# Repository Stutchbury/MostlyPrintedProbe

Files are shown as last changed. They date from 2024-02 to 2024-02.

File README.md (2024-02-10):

# A Mostly Printed Probe
A mostly printed kinetic probe for CNC machines that can be fully 3D printed (or turned on a lathe) and requires no soldering.

>If you can't make it accurate, make it adjustable.

3D printing accuracy is often hard to achieve, especially on a variety of printers, but this probe has been designed to work within the those accuracy contraints and has proven to provide remarkable repeatability:

Mostly Printed Probe first test (https://www.youtube.com/embed/06nPOA94Pbk)

After my 21 year old ebay 'bargain' Renishaw gave up the ghost, I needed a probe quickly to continue developing my [CNC Probe Interface](https://github.com/Stutchbury/CNCProbeInterface) so designed one to turn on the lathe but the test 3D printed version worked so well, it is now an official side project...

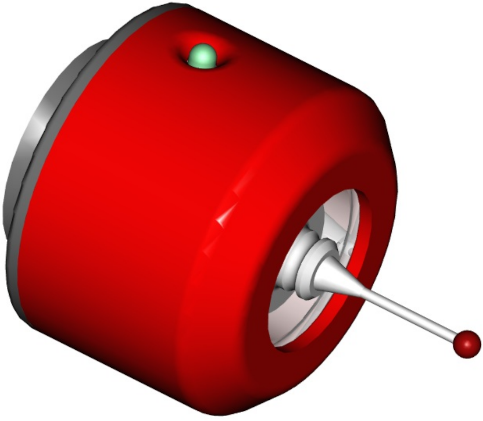
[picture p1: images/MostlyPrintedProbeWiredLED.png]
MostlyPrintedProbeWiredLED


With the exception of the 3mm diameter pins and the stylus, all of this probe is able to be FDM printed - even the spring is made from a length of filament! Only one part (the top) requires supports.

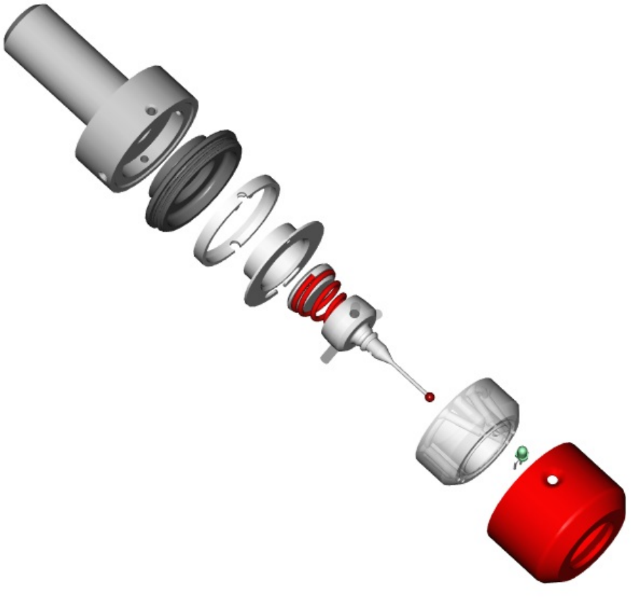
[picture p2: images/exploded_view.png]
MostlyPrintedProbeExploded


The 25mm/30° taper in the top allows concentricity to be tuned in on a mandrel while the tapered interface between body and sleeve ensure concentricity is maintained. 

There are two different bodies - one is wired only and the second can also accommodate a 3mm LED (single or bi-colour). The non-LED version requires no soldering.

This is the first build, it is fairly compact at 38mm diameter x 28mm tall. 

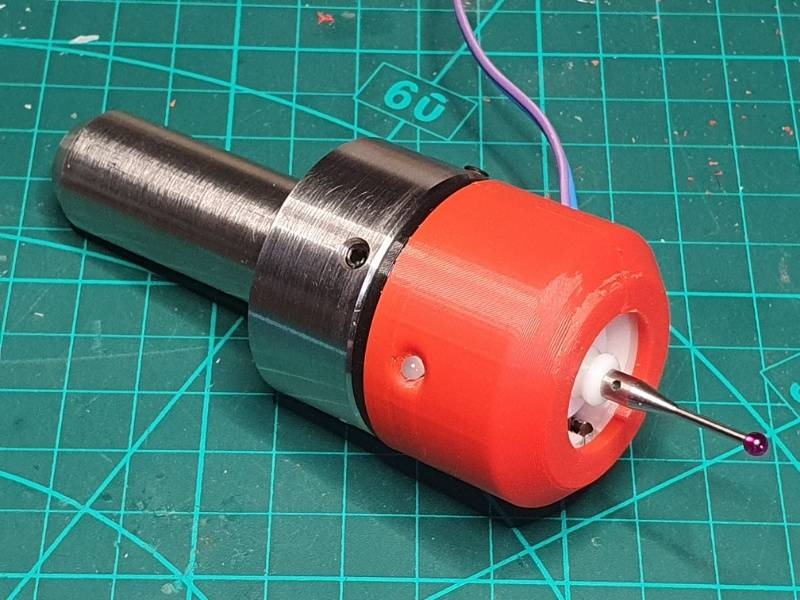
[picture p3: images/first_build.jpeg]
first buid


As with all mechanical kinetic probes, this will work best with a [resistive switching interface](https://github.com/Stutchbury/CNCProbeInterface) but will also work fine as a plain old NC (normally closed) switch.

## Materials & Tools Required

A quick list of things you'll need - I will create a proper print/build guide VSN.

- **Pins** - I have used 3mm tungsten carbide rods, but any decently conductive metal would work and is probably a lot easier to cut. Search for "3mm dowel pins" for pre-cut hardened steel ones.

  - 9off 3mm diameter by 11.5mm - 12mm length.

- **Filament** - I used plain old PLA on a rather old & tired Ender 3.

- **Accurate 3mm drill** or reamer (measure your drills, they vary a lot).

- **M3 tap** - to fit the stylus and optionally the spring tensioner.

- **Thin stranded wire** - as fine as you can. I stripped out a ribbon cable but old USB charging cables are a good source.

All the STLs are available [here](stl/). There are also 12mm and 3/4" example mandrels for fitting into your spindle. These enable concentricity to be tuned in.

## Slicing and Printing

A slicing and printing guide is available [here](docs/PRINTING.md).

## Assembly

The [assembly guide](docs/ASSEMBLY.md) is curently a work in progress.

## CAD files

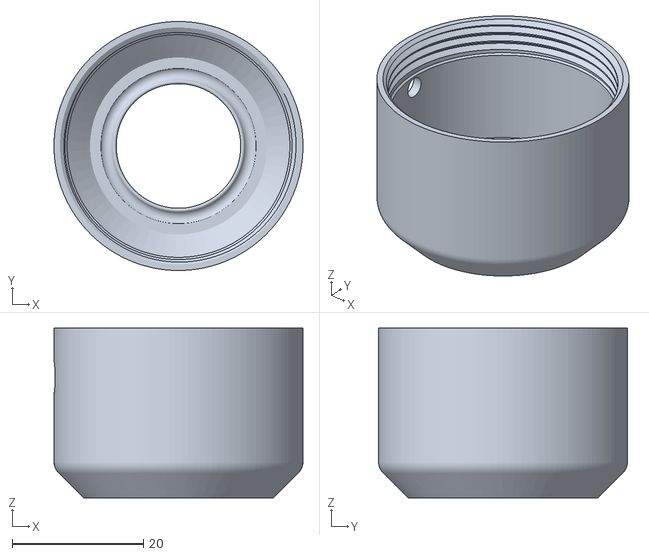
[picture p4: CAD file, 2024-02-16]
stl/MostlyPrintedProbe-PartMainBodyWired.stl
38.0 x 38.0 x 25.9

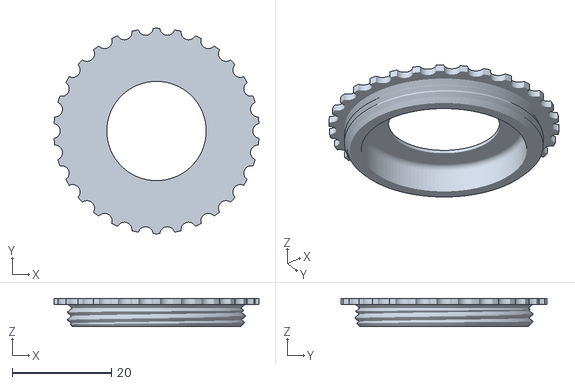
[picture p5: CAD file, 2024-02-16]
stl/MostlyPrintedProbe-PartTestExternalThread.stl
41.3 x 41.4 x 5.70

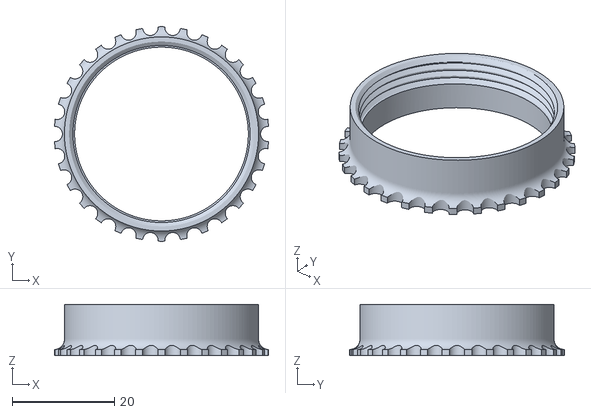
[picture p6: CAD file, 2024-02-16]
stl/MostlyPrintedProbe-PartTestInternalThread.stl
41.9 x 42.0 x 10.0

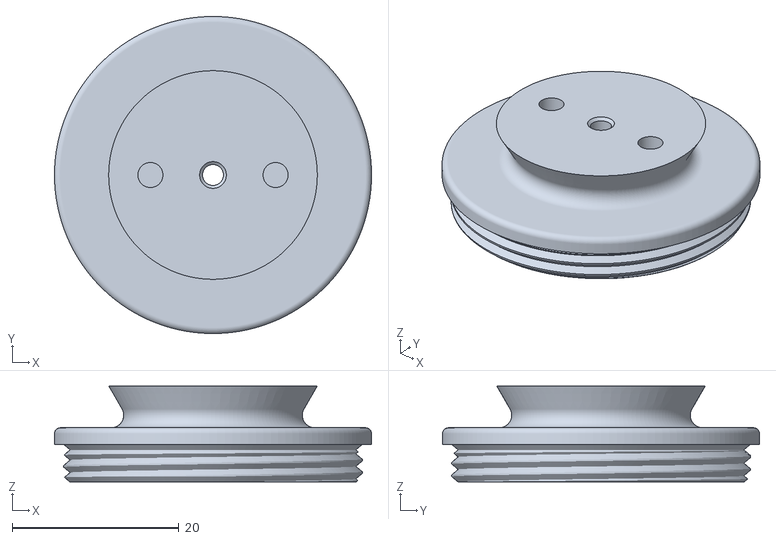
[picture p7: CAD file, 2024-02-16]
stl/MostlyPrintedProbe-PartTop.stl
38.0 x 38.0 x 11.5

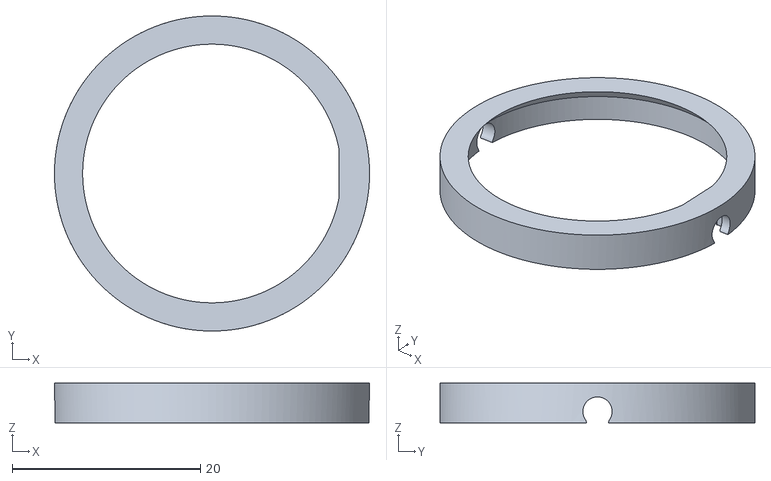
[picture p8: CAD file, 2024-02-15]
stl/MostlyPrintedProbe-PartSpacerWired.stl
33.5 x 33.5 x 4.20

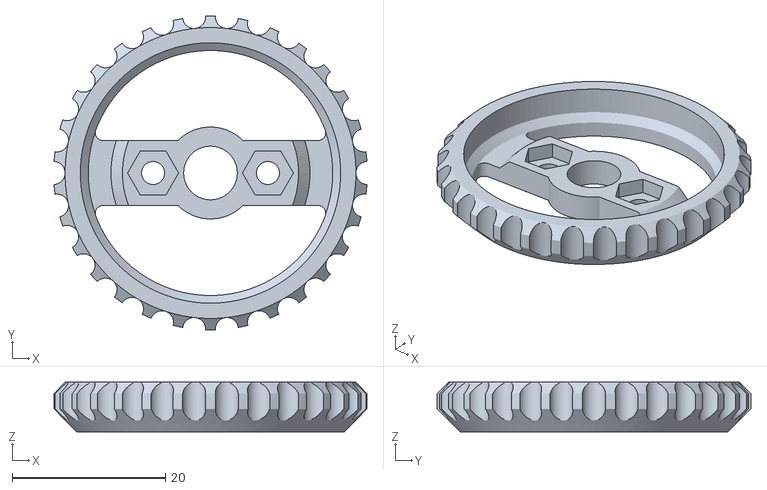
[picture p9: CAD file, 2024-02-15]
stl/MostlyPrintedProbe-ParLidSpanner.stl
40.9 x 41.0 x 6.50

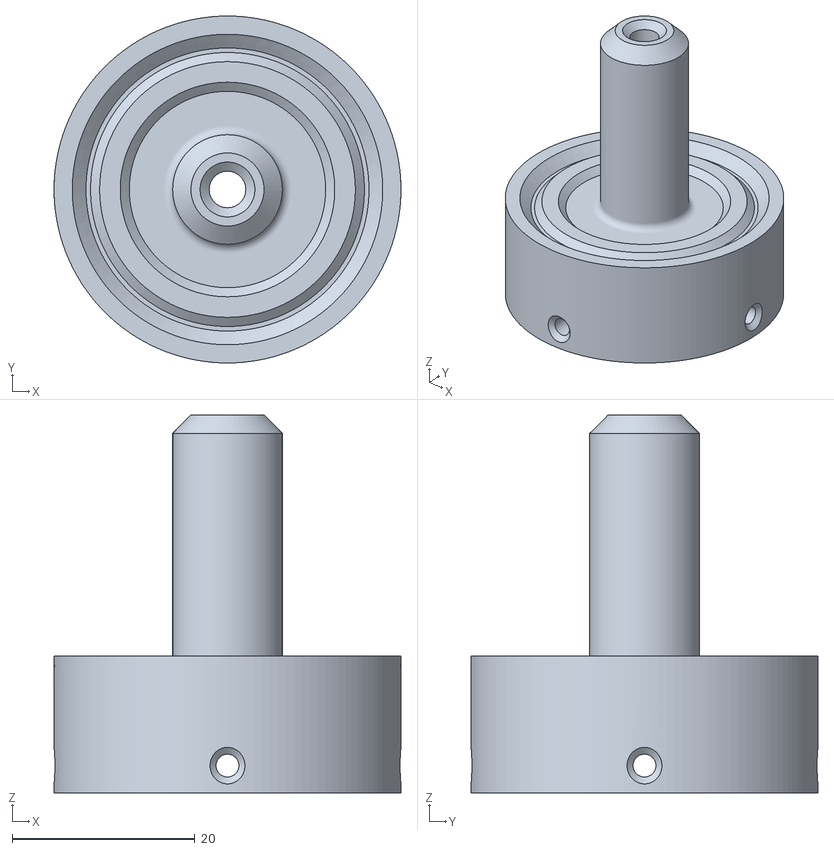
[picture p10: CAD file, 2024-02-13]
stl/MostlyPrintedProbe-PartSpindleMandrel-12mm.stl
38.0 x 38.0 x 41.4

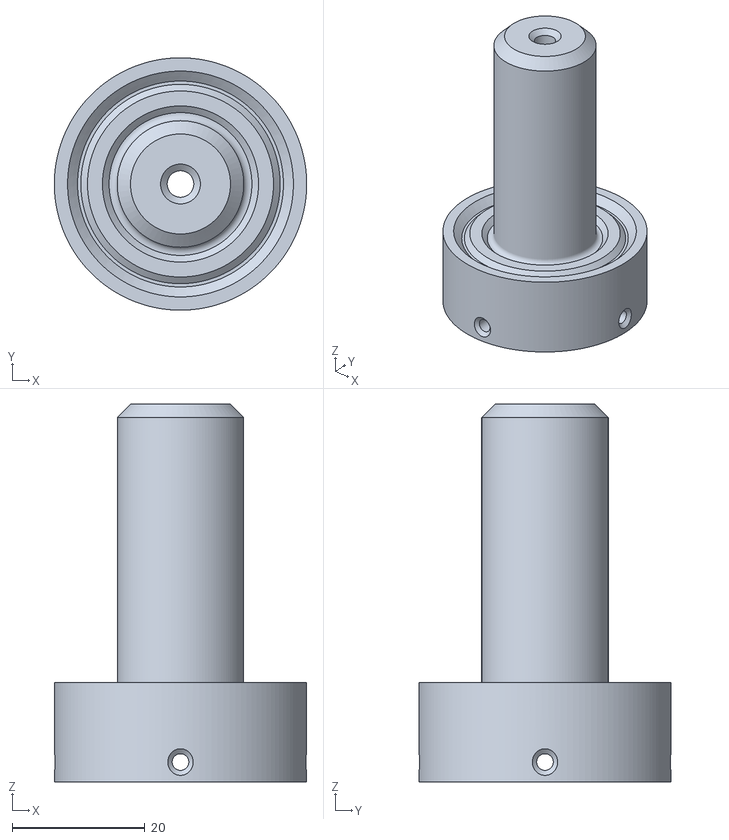
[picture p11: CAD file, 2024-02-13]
stl/MostlyPrintedProbe-PartSpindleMandrel-TTS.stl
38.0 x 38.0 x 56.9

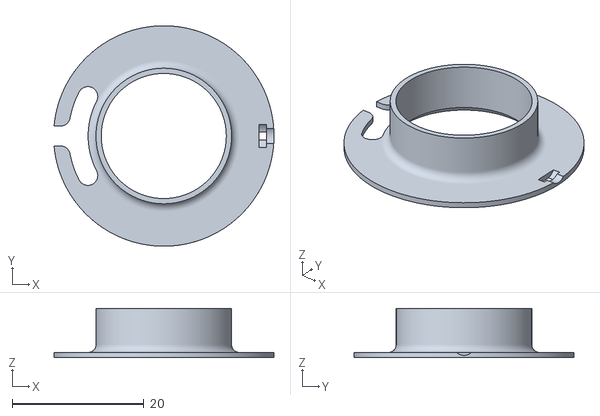
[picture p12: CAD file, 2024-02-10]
stl/MostlyPrintedProbe-PartPinsCover.stl
33.4 x 33.5 x 7.50

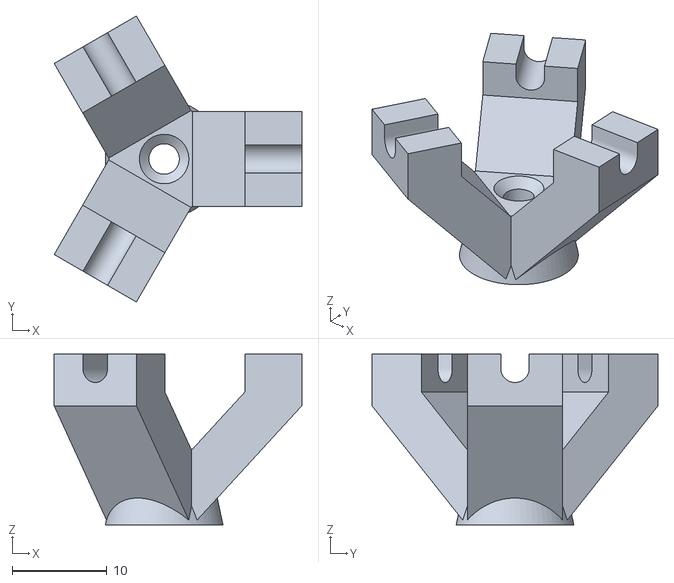
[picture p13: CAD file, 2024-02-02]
stl/MostlyPrintedProbe-PartSpiderTappingTool.stl
26.1 x 30.1 x 18.0

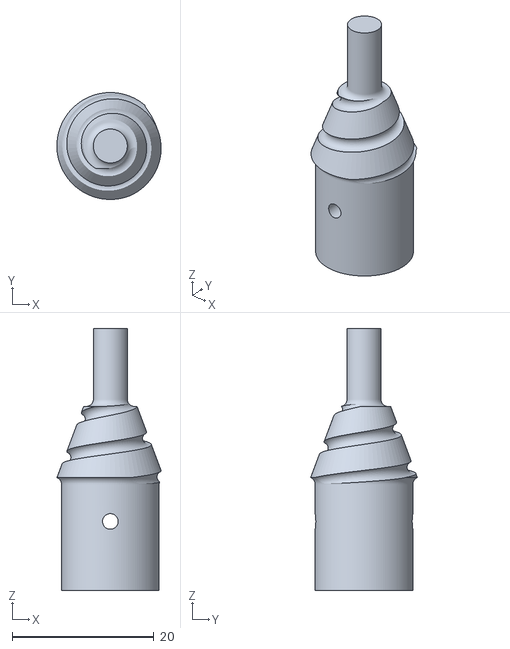
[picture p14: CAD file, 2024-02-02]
stl/MostlyPrintedProbe-PartSpringMandrel.stl
14.7 x 15.1 x 37.0

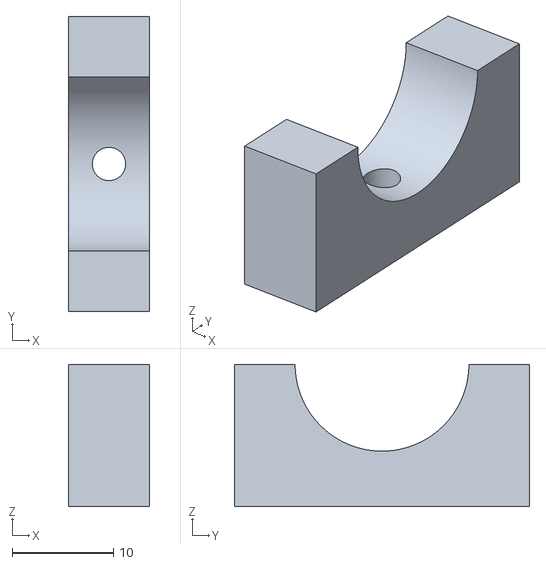
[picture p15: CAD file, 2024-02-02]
stl/MostlyPrintedProbe-PartSpiderPinTool.stl
8.00 x 29.2 x 14.1

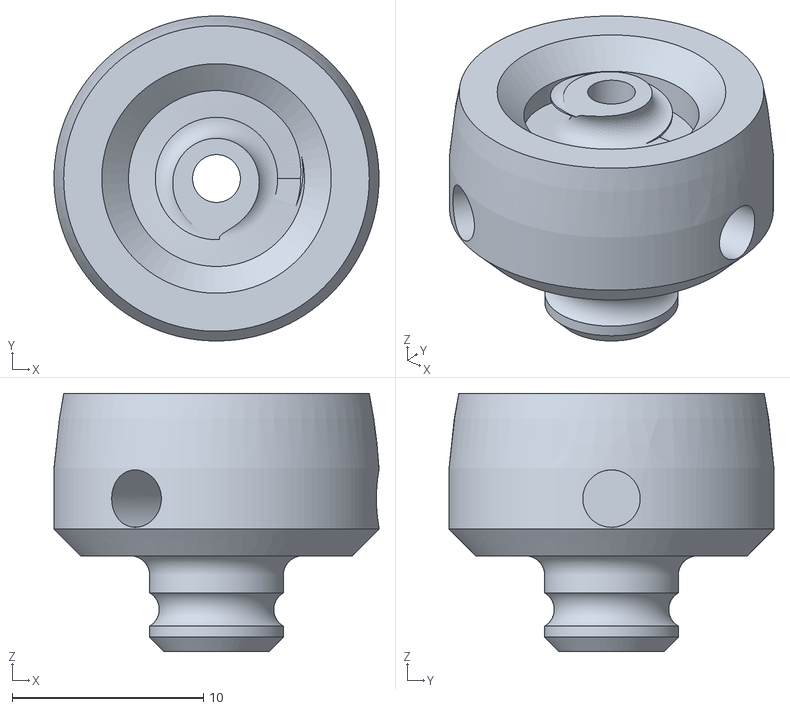
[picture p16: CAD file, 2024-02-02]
stl/MostlyPrintedProbe-PartSpider.stl
17.0 x 17.0 x 13.5

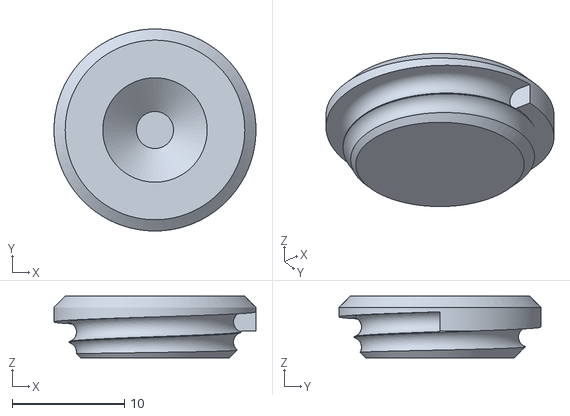
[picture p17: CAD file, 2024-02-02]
stl/MostlyPrintedProbe-PartSpringTop.stl
18.0 x 18.0 x 5.50

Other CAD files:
stl/MostlyPrintedProbe-PartMainBodyWiredLED.stl

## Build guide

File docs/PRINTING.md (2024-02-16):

# Printing the Mostly Printed Probe

This guide is for FDM printing the Mostly Printed Probe. All models are [here](../stl).

## Tolerances

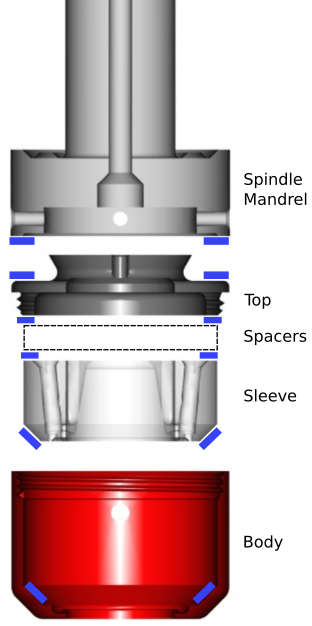
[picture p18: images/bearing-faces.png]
bearing face


Most of the models have fairly relaxed tolerances with the accuracy of the probe being defined by the bearing faces shown above in blue - in particular, the 45° faces inside the body and on the bottom of the sleeve.

### Threads

Yes, the large threads work just fine in a 3D printed model!

The M3 threads in the lid (for the spring tension) and spider (for the stylus) need to be carefully cut with a tap. A [threading guide](../stl/MostlyPrintedProbe-PartSpiderTappingTool.stl) is provided to help align the tap with the spider.

The main M36 x 1.5mm thread (that secures the top to the body and compresses all the bearing faces) can provide some challenges. The thread itself has a generous tolerance built in, but there are many factors to acheiving a good thread but all can be resolved in the slicer.

Note: The main threads are now at an 80° thread angle rather than the standard 60° - this helps printing overhangs without support.

#### Shrinkage
The first lid & body I printed fitted perfectly (yes, I know, I'm was as surprised as you are) but when I re-printed the body in red, the diameter shrank. The same filament from the same manufacturer but in black, did not.

I have created two test nodels that I suggest are printed with your filament of choice. There is an [internal thread](../stl/MostlyPrintedProbe-PartTestInternalThread.stl) to represent the main body and an [external thread](../stl/MostlyPrintedProbe-PartTestExternalThread.stl) for the lid.

Print the internal thread (or the main body if you're feeling confident) first and then match the external thread to it. If your filament is similar to mine, it should fit first time, otherwise, scale and re-print the external thread and apply these settings to the lid slicing. Clean up the seam inside the thread hollows and lubricate with a soft pencil to prevent the stickyness of some filaments.

The test prints have grips on the perimeter but if you get the real lid stuck, there's a [spanner](../stl/MostlyPrintedProbe-ParLidSpanner.stl) for it!

#### Sagging
If your filament is too hot, the thread overhangs ~~(they are at 60°)~~ can sag a little, so playing with the temperature can help. The new 80° thread angle should significantly mitigate this issue.

#### Sticktion
Some filaments, especially shiny PLA, have a nasty habit of sticking to each other. Your thread may be perfect but the think just wants to stick. Matt PLA seems to work much better.

Use graphite (a soft pencil) to lubticate the threads and make sure the seams is cleaned out of the thread grooves.

Use the lid spanner to free a stuck thread.

#### Cross threading

An M36 x 1.5mm thread is *really* easy to cross thread - especially when the wires are not allowing the spacers to sit flat. Check the thread works wih just the lid and body (I'm sure you would anyway...) but be exceedingly careful as once cross threaded, plastic threads are very difficult to 'get back'. If it doesn't start easily & reliably, then final assembly gets a bit fractious.

## Slicing & Printing

I'm using Cura at 0.2mm layer height. Sometimes the slicer will report errors in the STLs but then automagically repair them and print just fine. I'm working on resolving this but as everything prints OK, it is a little down the priority list.

**A Note on Seams:** Unless you are able to truly hide your Z seam (ie no blobs), I recommend having a single seam that can be filed or scraped flat where required.

Unless otherwise specified, I am using 4 walls and the default infill. Only one part need supports.

### Sleeve 

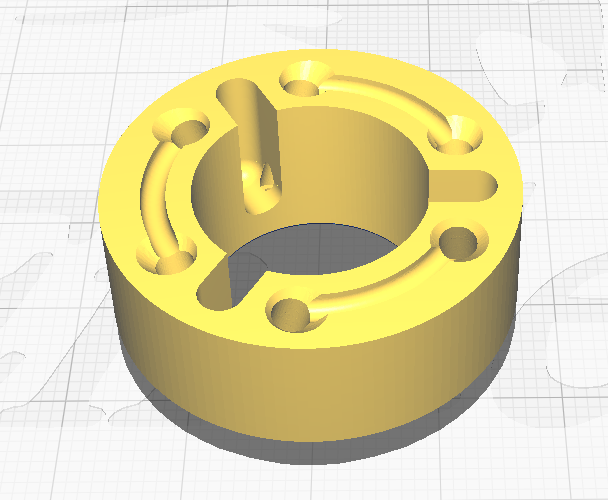
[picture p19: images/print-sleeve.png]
print sleeve


- Filament required: 7g, 2.25m
- Support: Not required

The pin holes are (in theory) exactly 3mm diameter - they can by adjusted with 'Hole Horizontal Expansion' in Cura but unless they are coming out loose, then leave as is because we'll be reaming or drilling them in the assembly.

The small holes in the underside are to ease the rmoval of the pins, so if you think you might need that, clean them out too.

File the seam away on the lower 45° outer face.

### Main Body

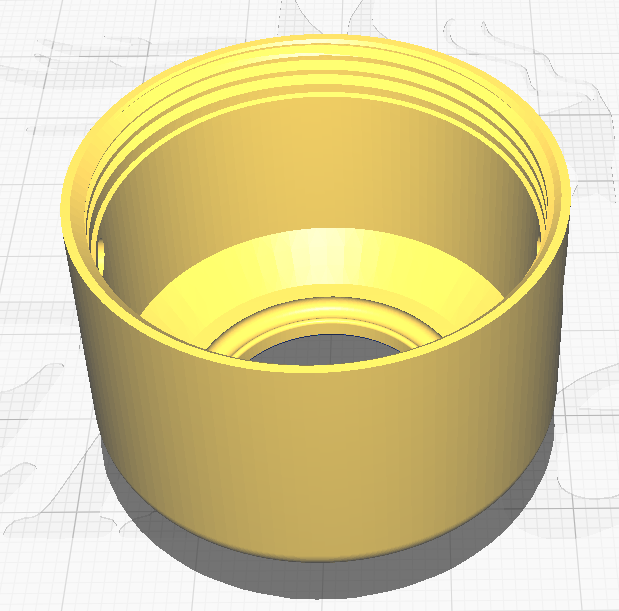
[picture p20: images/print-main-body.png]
main body


- Filament required: 8g, 2.58m
- Support: Not required

There may be a little sagging at the top of the cable/LED holes but these are easily resolve with a 3mm drill.

Ensure in the preview there are no odd concentric gaps in the walls - they should be solid.

Scrape the seam away on the inner 45° face. A sharp flat-bladed screwdriver works well.

### Top

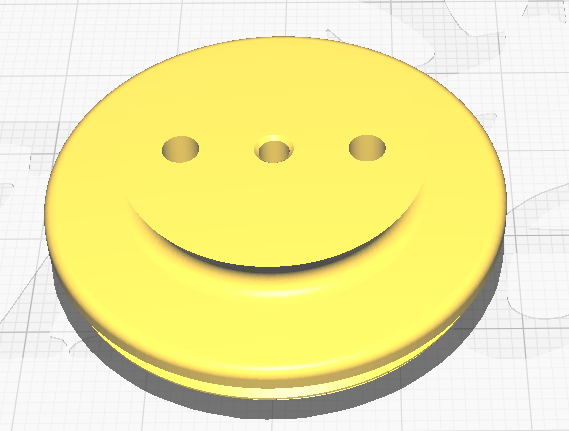
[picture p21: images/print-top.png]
top


- Filament required: 5g, 1.7m
- Support: **Required**

An apparently happy part, but despite this, needs support. We are printing in this orientation because the bottom of the thread and the wide upper face need to be parallel. The underside edge at the top of the threads shouldn't actually touch the main body when screwed in.

### Spider

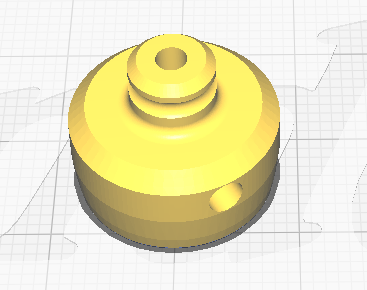
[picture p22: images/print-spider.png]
spider


- Filament required: 2g, 0.69m
- Support: Not required
- Print Orientation: Upside down

I printed this solid (eg 10 walls) as the three pins will try to split the layers as you push them in.

### Pins Cover

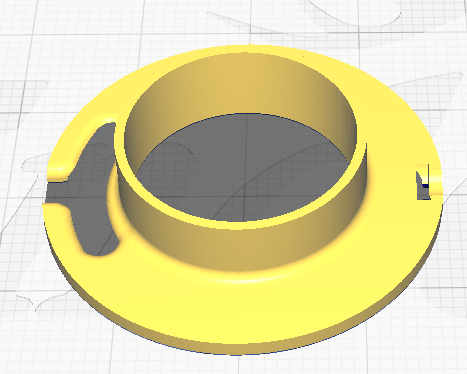
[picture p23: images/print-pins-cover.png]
pins cover


- Filament required: 1g, 0.35m
- Support: Not required

Check the thickness of the wide lip - it should be ~0.8mm-1mm (4 layers). If your printer squishes the first layer, you may need to print a slightly taller spaces.

### Spacer

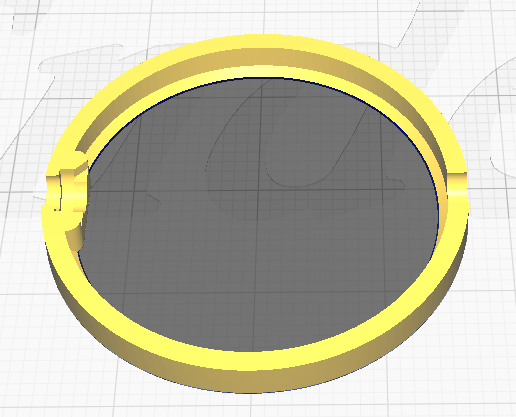
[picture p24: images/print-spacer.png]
spacer


- Filament required: 1g, 0.22m
- Support: Not required

Every project needs a spacer! No supports required but print upside down.

If your top tightens on the body before clamping the sleeve, then scale this part in Z as required.

This part also holds the (optional) LED in place.

### Spring Top

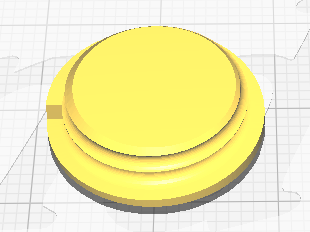
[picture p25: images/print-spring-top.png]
spring top


- Filament required: 1g, 0.35m
- Support: Not required
- Print orientation: Upside down

This sits on top (well, screws into) the top of filament-made spring to 'level out' the coils.

## Tools

These are utility prints to assist with the assembly.

### Top Spanner

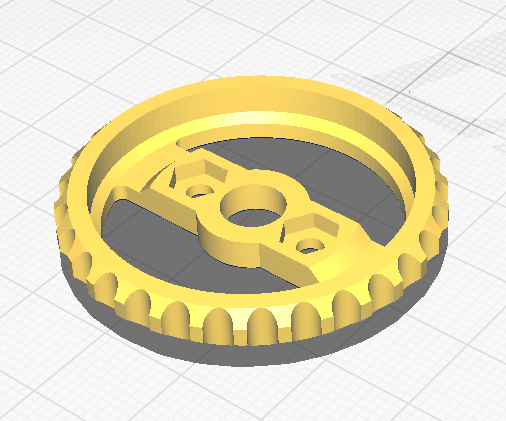
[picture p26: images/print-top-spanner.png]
Top Spanner


- Filament required: 3g, 1.08m
- Support: Not required

Add two M3 x 8mm screws and nuts to create a pin spanner and help unscrew the top from the base (when, not if, it sticks).

#### Spider Pin Guide

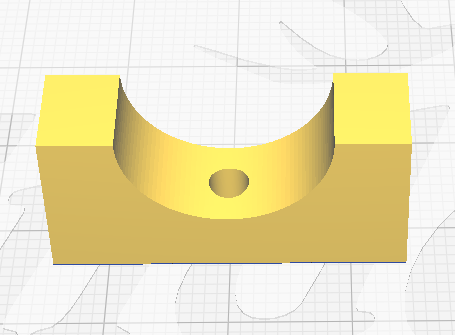
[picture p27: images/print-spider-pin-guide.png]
spider pin guide


- Filament required: 2g, 0.73m
- Support: Not required

Used to ensure the spider's pins stick out just the right amount.

#### Spider Threading Guide

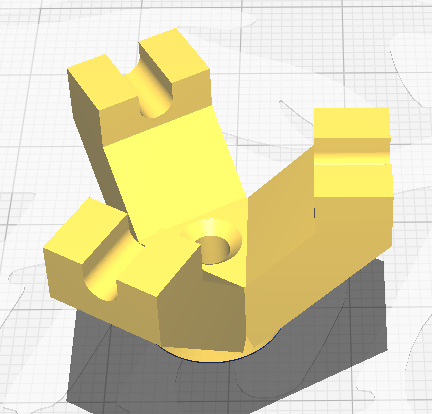
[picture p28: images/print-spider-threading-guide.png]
spider threading guide


- Filament required: 3g, 1.02m
- Support: Not required

Sits on the spider's pins to provide a guide for the M3 tap.

#### Spring Mandrel

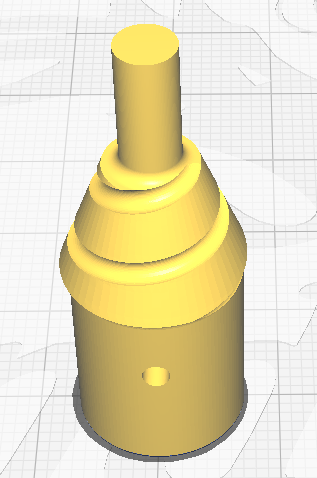
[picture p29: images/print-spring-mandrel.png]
spring mandrel


- Filament required: 3g, 0.94m
- Support: Not required

Used to wrap filament and 'set' using hot/cold water.

If you have any higher temperature filament, this might benefit, but I used PLA.

### Spindle Mandrels

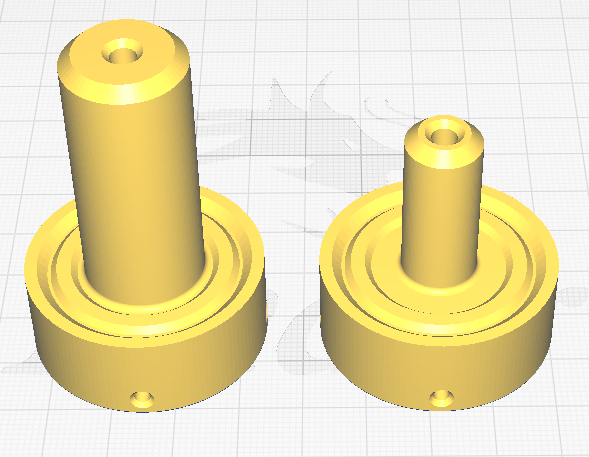
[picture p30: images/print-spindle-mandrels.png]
Spindle mandrels


- Filament required: 12-17g 4.09-5.76m
- Support: Required

Not strictly part of the Mostly Printed Probe but provided for testing and modelling. Ideally these shoulb be turned out of metal as this is the bit that is regularly tightened into the spindle.

The four M3 threads allow you to tune in concentricity of the stylus.

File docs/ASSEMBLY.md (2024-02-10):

# Assembling the Mostly Printed Probe

This document is a work in progress - it takes a lot longer to document the assmbly than it does to actualy do it...

Once you have all the parts printed, it should be fairly self explanatory but here's a heads up on wiring the contacts:

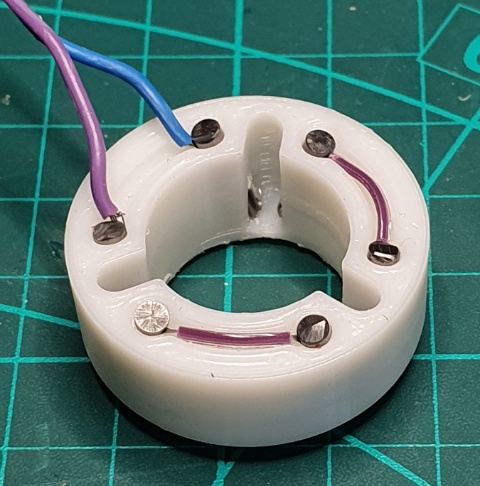
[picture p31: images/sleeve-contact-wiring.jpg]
contact wiring


*Very* thin stranded wire is held in place by the pins (if you don't want/need an LED, then no soldering is required).

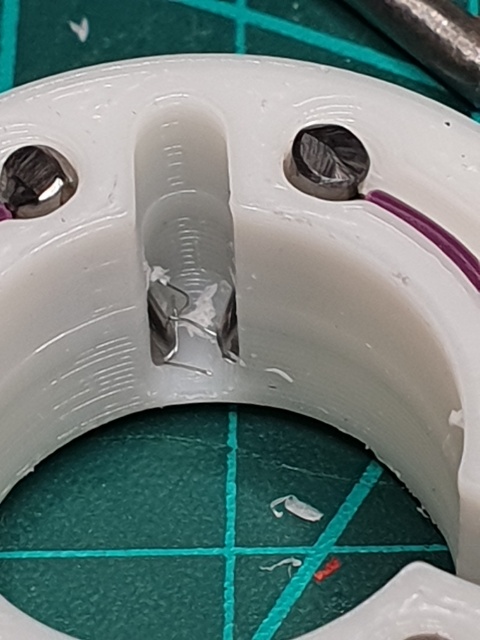
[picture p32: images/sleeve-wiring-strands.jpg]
contact wiring


Just make sure you pick out any loose strands or bits of plastic from between the pins.

Note: for newer versions (anything after v1.0..0), make sure both jumper wires and pins are flush or below the top surface - some of my pins in the picture above are a little long. The connector wires have a slot cut for them in the pin cover.

## Making the Spring

___WARNING!___ 

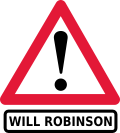
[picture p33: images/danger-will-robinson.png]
Dager
 

___****** DO THIS AT YOUR OWN RISK! ******___

**Making the spring involves *very* hot water and a risk of scalding - do not attempt unless you are properly protected.**

For the spring, warm about a foot (30cm) of filament in hot water, poke it through the hole at the bottom, wrap two turns on the flat, then up the helix and another two or three turns on the narrow flat section. Depending on how old/inflexible your filamant is, you may need to keep running under hot water.

Once fully wound (it will try to spring off), wrap tightly in painters tape (thanks Chris NS), hold onto the ends and dunk the turned parts into near-boiling water for a second or so* then under a cold tap. This will raise the filament to (or near) it's plastic temperature and then set it.

\* you can tell when it is 'done' by gently pulling one of the loose ends - as you feel it start to stretch, it is ready for a cold dunk.

If you haven't wrapped with painters tape, it is safer to dunk & chill one end at a time, so you can hold a cold end of the mandrel.

The narrow end will probably loosen but this can be re-dunked and tightened by holding on to the cold end of the mandrel and the cold end of the filament.

***Unless you have asbestos hands, wear protective gloves and take all necessary precautions.***

Once again: ___****** DO THIS AT YOUR OWN RISK! ******___

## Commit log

2024-02-02 Initial upload
    [MostlyPrintedProbe-PartMainBodyWired.stl, MostlyPrintedProbe-PartMainBodyWiredLED.stl, MostlyPrintedProbe-PartPinsCover.stl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]
2024-02-04 Update images to use current models
2024-02-05 Add example spindle mandrels
    [MostlyPrintedProbe-PartSpindleMandrel-12mm.stl, MostlyPrintedProbe-PartSpindleMandrel-TTS.stl]
2024-02-05 Slicing & Printing Guide first draft
2024-02-05 Assembly doc placeholder
2024-02-05 Correct the thread pitch description...
2024-02-05 Add filament weight/lengthj requirements.
2024-02-10 Updated pins cover and spacer
    [MostlyPrintedProbe-PartPinsCover.stl, MostlyPrintedProbe-PartSpacerWired.stl]
2024-02-13 Slightly taller concentric adjustment wedge
    [MostlyPrintedProbe-PartSpindleMandrel-12mm.stl, MostlyPrintedProbe-PartSpindleMandrel-TTS.stl, MostlyPrintedProbe-PartTop.stl]
2024-02-13 Move pin eject holes to make first layer easier to print.
2024-02-15 Add top pin spanner
    [MostlyPrintedProbe-ParLidSpanner.stl]
2024-02-15 Add 0.5mm to spacer height
    [MostlyPrintedProbe-PartSpacerWired.stl]
2024-02-16 Now using custom 80° thread angle for easier printing
    [MostlyPrintedProbe-PartMainBodyWired.stl, MostlyPrintedProbe-PartMainBodyWiredLED.stl, MostlyPrintedProbe-PartTestExternalThread.stl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]
